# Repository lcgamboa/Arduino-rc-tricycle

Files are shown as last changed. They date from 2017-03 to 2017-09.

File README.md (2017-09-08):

# Simple and cheap DIY arduino rc tricycle controlled by smartphone  

Arduino code for rc tricycle

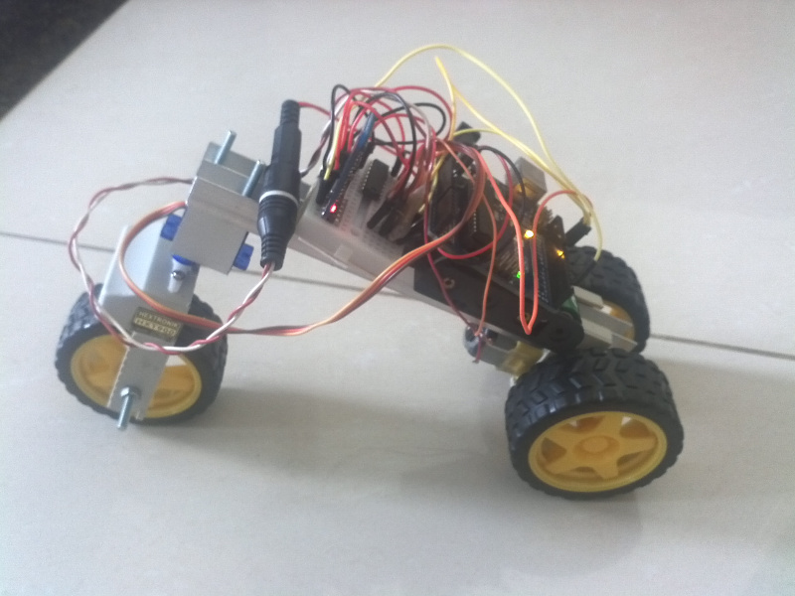
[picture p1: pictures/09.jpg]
Tricycle


video    	     https://www.youtube.com/watch?v=XjhdBfRUhjk

Android App          http://ai2.appinventor.mit.edu/?galleryId=4613735615037440

## Parts

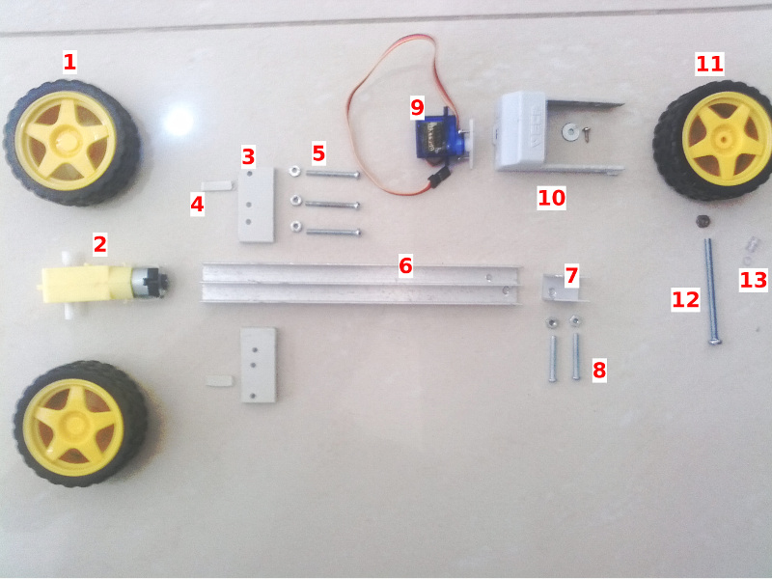
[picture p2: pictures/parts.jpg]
Tricycle Parts


| Number |Quantity  | Size | Description | Descrição|
|---|---|---|---|---|
|1 | 2 | 6.8x2.5 cm (DiameterxWidth)  |whell | Roda |
|2 | 1 | 7x2x2 cm |motor with reduction box| Motor com caixa de redução|
|3 | 2 | 2x2.4x0.15 cm  |plastic support (1)| Suporte de plástico (1)|
|4 | 2 | 1x0.5x0.15 cm |spacer (1)| espaçador (1)|
|5 | 3 | 3x0.2 cm |screw and nut | parafuso e porca|
|6 | 18 cm  | 2.2x1.3 cm |aluminum rail | trilho de alumínio|
|7 | 2 cm | 1.5x2.5cm |aluminum profile U-frame | cantoneira perfil U de alumínio |
|8 | 2 | 1x0.2 cm |screw and nut | parafuso e porca|
|9 | 1 | 3x1x3 cm |micro servo | micro servo |
|10 | 1 | 7x4 cm |plastic fork (2)| garfo plástico (2)|
|11 | 1 | 6.8x2.5 cm (DiameterxWidth) |whell with hole | Roda com buraco (3) |
|12 | 1 | 5x0.3 cm |screw and nut | parafuso e porca|
|13 | 1 | 0.7 and 0.1 cm |axis spacer | espaçador de eixo (4)|

* (1) Made from cut 2 cm of desktop blank slot cover. Size 2x4.2 cm. / Feito de um corte de 2 cm de tampa de baia de computador. Tamanho 2x4,2 cm.

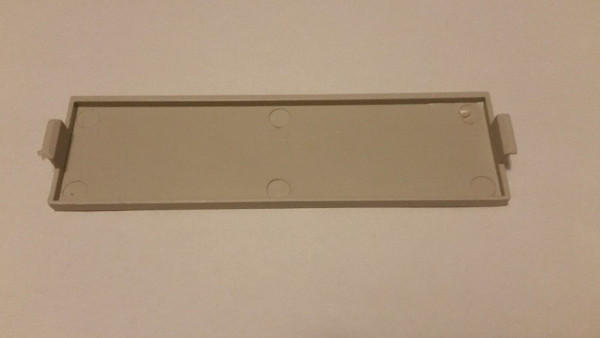
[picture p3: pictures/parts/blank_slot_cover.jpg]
slot cover


* (2) Made from a burned out electronic balast plastic box. Size 7x4 cm. / Feito de uma caixa plástica de reator eletrônico queimado. Tamanho 7x4 cm.

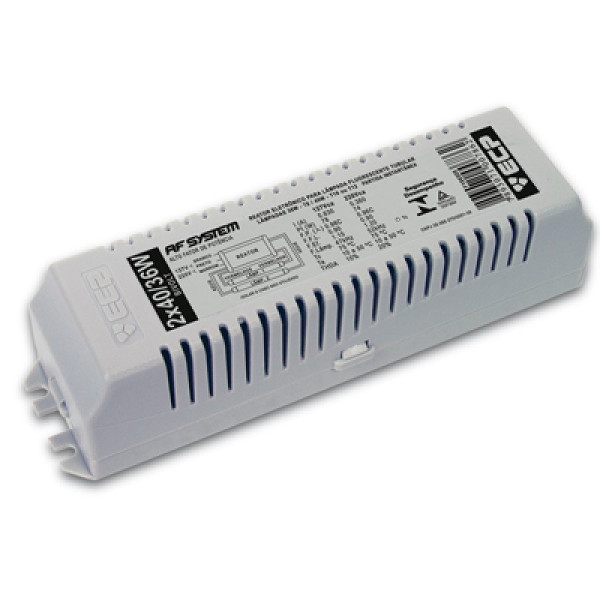
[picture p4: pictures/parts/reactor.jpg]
fork reactor


* (3) Same as item 1 with a hole of 3 mm diameter.  / Mesmo item que o 1 com um furo de 3mm de diâmetro.

* (4) Made from 1mm and 7mm of aquarium air tube. / Feito de magueira de aquário com 1mm e 7mm.

## Circuit

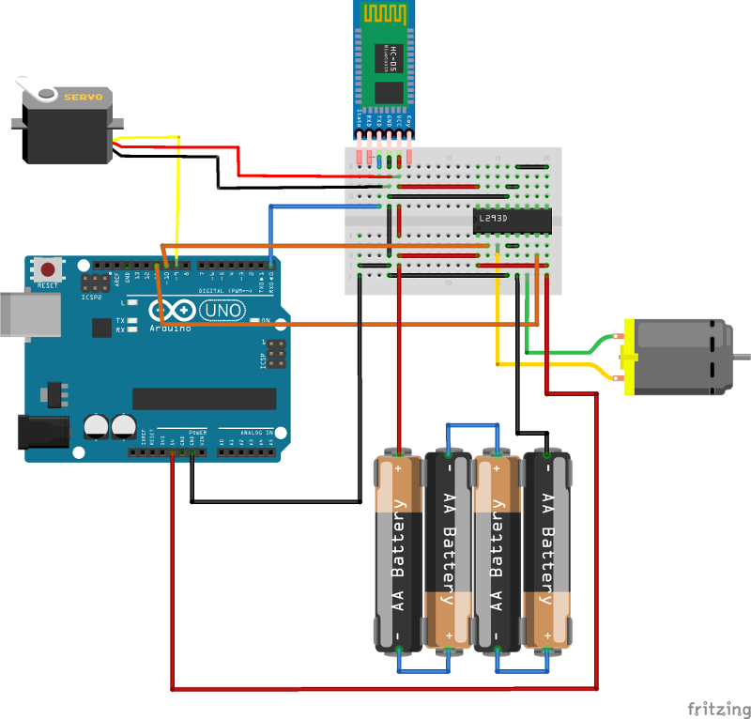
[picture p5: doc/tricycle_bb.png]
Circuit circuit


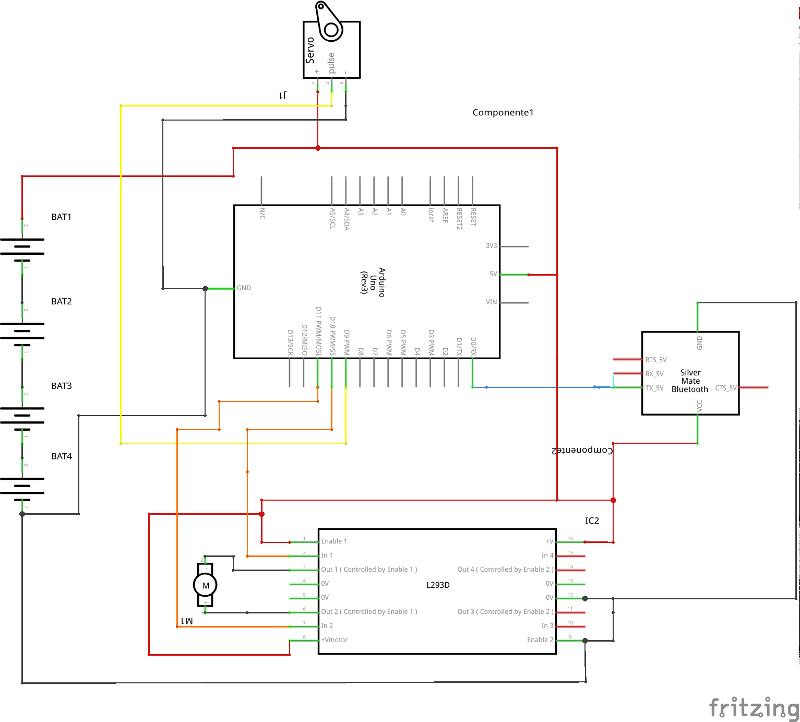
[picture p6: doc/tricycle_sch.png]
Schematic schematic


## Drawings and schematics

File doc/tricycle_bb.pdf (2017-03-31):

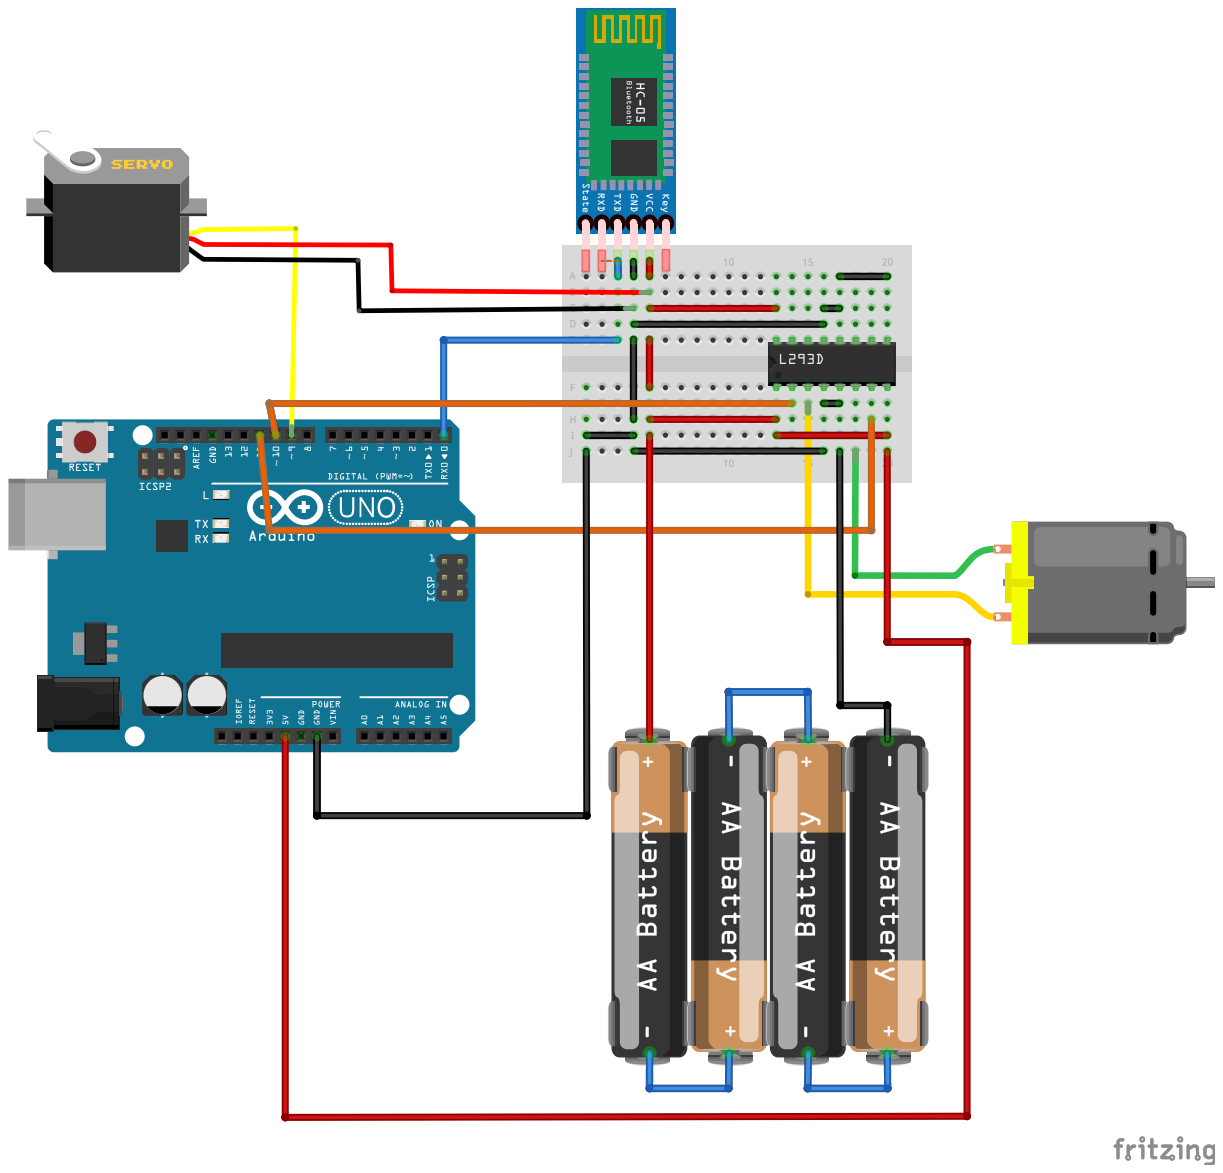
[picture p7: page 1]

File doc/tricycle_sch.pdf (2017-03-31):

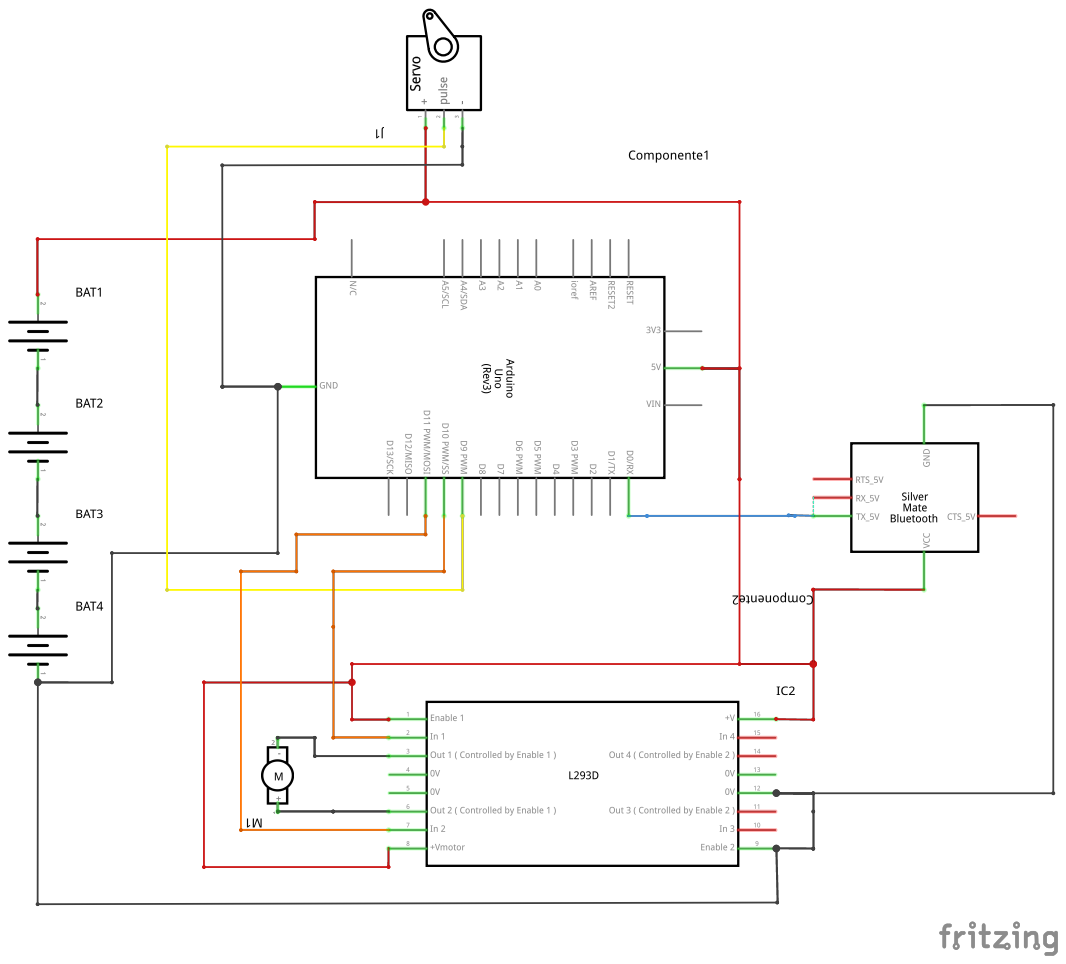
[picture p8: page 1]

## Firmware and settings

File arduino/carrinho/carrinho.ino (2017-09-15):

/* Simple and cheap DIY arduino rc tricycle controlled by smartphone 

 modified 31 March 2017
 by lcgamboa@yahoo.com
 https://www.youtube.com/watch?v=XjhdBfRUhjk
*/

//code for arduino uno

#include <Servo.h>
#include <VoltageReference.h>

Servo myservo;  // create servo object to control a servo

VoltageReference vBat;

#define center 94 //angle to align center position

void setup() {
  pinMode(10, OUTPUT); //Foward H bridge
  pinMode(11, OUTPUT); //Backward H bridge
  
  myservo.attach(9);  // Direction servo
  myservo.write(center);

  digitalWrite(10, LOW);
  digitalWrite(11, LOW);

  vBat.begin();          
  Serial.begin(9600); //Bluetooth connection
}

void loop() {

  if (Serial.available() > 0) { //if receveid bluetooth command
     unsigned char cmd = Serial.read();

     switch(cmd)
     {
       case 'w'://frente - foward
         digitalWrite(10, HIGH);
         digitalWrite(11, LOW);
         break; 
       case 'r'://parar - stop
         digitalWrite(10, LOW);
         digitalWrite(11, LOW);
         break; 
       case 's'://trás - backward
         digitalWrite(10, LOW);
         digitalWrite(11, HIGH);
         break; 
       case 'd'://direita  - right
         myservo.write(140); //angle in degrees
         break; 
       case 'a'://esquerda  -left
         myservo.write(40); //angle in degrees
         break; 
       case 'q'://centro  -center
         myservo.write(center); 
         break; 
       case 'b'://v battery
         Serial.println(vBat.readVcc());  
       default:
         break; 
     }

  }
                
    
}

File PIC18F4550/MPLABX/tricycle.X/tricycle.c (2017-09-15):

#include<xc.h>
#include"serial.h"
#include"servo.h"
#include"atraso.h"

unsigned char centro = 90;

void setup() {
    serial_init();//default 9600
    TRISCbits.RC7=1;
    servo_init();
    TRISDbits.TRISD1 = 0;
    TRISDbits.TRISD2 = 0;
    PORTDbits.RD1 = 0;
    PORTDbits.RD2 = 0;
    servo_pos(centro);
}

void loop() {
    switch (serial_rx(0)) {
        case 'd':
            servo_pos(180);
            break;
        case 'a':
            servo_pos(0);
            break;
        case 'q':
            servo_pos(centro);
            break;
        case 'w':
            PORTDbits.RD1 = 1;
            PORTDbits.RD2 = 0;
            break;
        case 's':
            PORTDbits.RD1 = 0;
            PORTDbits.RD2 = 1;
            break;
        case 'r':
            PORTDbits.RD1 = 0;
            PORTDbits.RD2 = 0;
            break;
	case 'b':
	    serial_tx_str("0000\n"); //Not implemented
	    break;    
    }
    

}

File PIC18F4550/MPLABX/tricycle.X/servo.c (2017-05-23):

/* ########################################################################

   PICsim - PIC simulator http://sourceforge.net/projects/picsim/

   ########################################################################

   Copyright (c) : 2014-2017  Luis Claudio Gambôa Lopes

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
   For e-mail suggestions :  lcgamboa@yahoo.com
   ######################################################################## */
#include"config.h"
#include<xc.h> 
#include"servo.h"


#define T0INI (unsigned int)(65536-(18e-3* _XTAL_FREQ/4.0 )/4.0)
#define T0INIH (unsigned char)((T0INI&0xFF00)>>8) 
#define T0INIL (unsigned char)(T0INI&0x00FF)

#define OUT PORTBbits.RB0
#define TOUT TRISBbits.TRISB0


unsigned char T0PULSEH;
unsigned char T0PULSEL;

void interrupt isr()
{
  if(INTCONbits.TMR0IF)//every ~= 15ms
  {
     if(OUT)
     {    
       OUT=0;  
       TMR0H=T0INIH;
       TMR0L=T0INIL;
     }
     else
     {
       TMR0H=T0PULSEH;
       TMR0L=T0PULSEL;         
       OUT=1;
     }
     INTCONbits.TMR0IF=0;
  }
  
}

void servo_init(void)
{
    //Configura TMR0
   T0CONbits.T08BIT=0;
   T0CONbits.T0CS=0;
   T0CONbits.PSA=0;
   T0CONbits.T0PS2=0;//divide por 4 
   T0CONbits.T0PS1=0;
   T0CONbits.T0PS0=1;

   TMR0H=T0INIH;
   TMR0L=T0INIL;
   
   servo_pos(90);
   
   INTCONbits.TMR0IF=0;
   INTCONbits.TMR0IE=1;
   INTCONbits.GIE=1;
   
   T0CONbits.TMR0ON=1;
   
   TOUT=0;
   OUT=0;   
}
    
 
void servo_pos(unsigned char value)//0 to 180
{
    unsigned int  T0PULSE;
    T0PULSE=(unsigned int)(65536-((0.5e-3+(2.0e-3*value/180.0) )* _XTAL_FREQ/4.0 )/4.0);
    T0PULSEH=(T0PULSE&0xFF00)>>8;
    T0PULSEL=(T0PULSE&0x00FF);   
}

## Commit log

2017-05-23 Pinguino and MPLABX PIC18F4550 support added
    [tricycle_pic.fzz]
2017-09-15 Battery voltage support

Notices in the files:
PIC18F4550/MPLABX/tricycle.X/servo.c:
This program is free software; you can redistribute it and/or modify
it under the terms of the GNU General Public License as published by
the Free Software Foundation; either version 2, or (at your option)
